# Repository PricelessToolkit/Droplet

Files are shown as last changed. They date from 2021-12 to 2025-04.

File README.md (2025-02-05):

🤗 Please consider subscribing to my [YouTube channel](https://www.youtube.com/@PricelessToolkit/videos)
Your subscription goes a long way in backing my work.



# Droplet
 ALL-IN-ONE Irrigation and monitoring system for ESPHome and Home Assistant.
 * Youtube How-To https://youtu.be/mCXTqONmpZk
 * Shop https://www.pricelesstoolkit.com

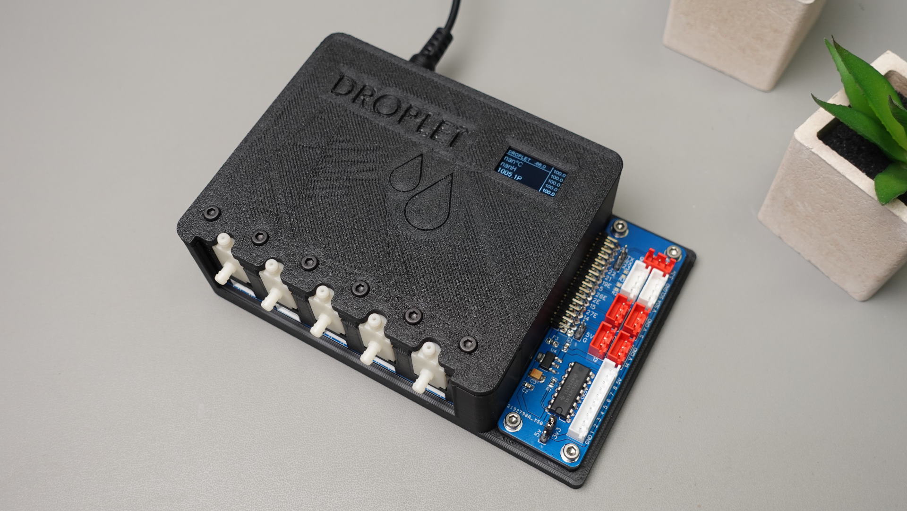
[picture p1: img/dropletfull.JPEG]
DROPLETFull
 

   ### Main Board

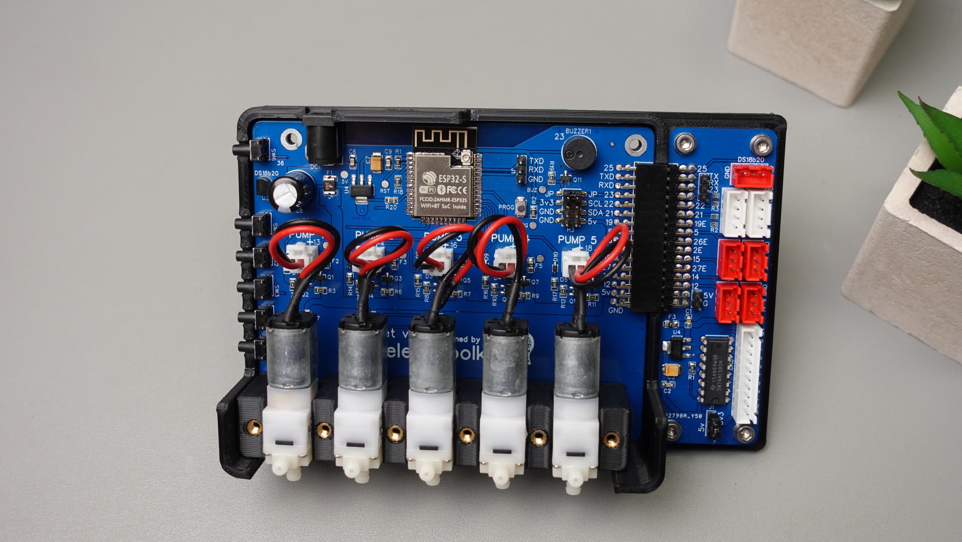
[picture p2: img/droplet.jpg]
DROPLET
 

 1. 5x Micro Pump outputs "5v"
 2. 5x Soil Moisture sensor inputs "Data-5v-GND" 'Data line pulled down with 1M ohm resistor' ( Data line MAX 3.3v !!!!! )
 3. Onboard Temperature sensor "DS18B20" https://esphome.io/components/sensor/dallas.html
 4. Onboard Buzzer "Buzzer port can be free up with jumper" https://esphome.io/components/rtttl.html?highlight=buzzer
 5. Breakout pins for connecting "i2c OLED Display" https://esphome.io/components/display/ssd1306.html?highlight=display
 6. 5x Buttons for manual Pumps controll
 7. 1x Button "Short press" for wake-up Oled "Long press" for general purpose. "2x Binary sensors available for HA"
 8. All pumps outputs and moisture sensor inputs have fuses
 9. Pins Which can be used "GPIO 19,5,26,2,15,27,14,12" and "1xi2c GPIO 21,22" "1xUART" "GPIO25 External port for DS18B20 TMP Sensor!!"
 
  ### Expansion Board v3

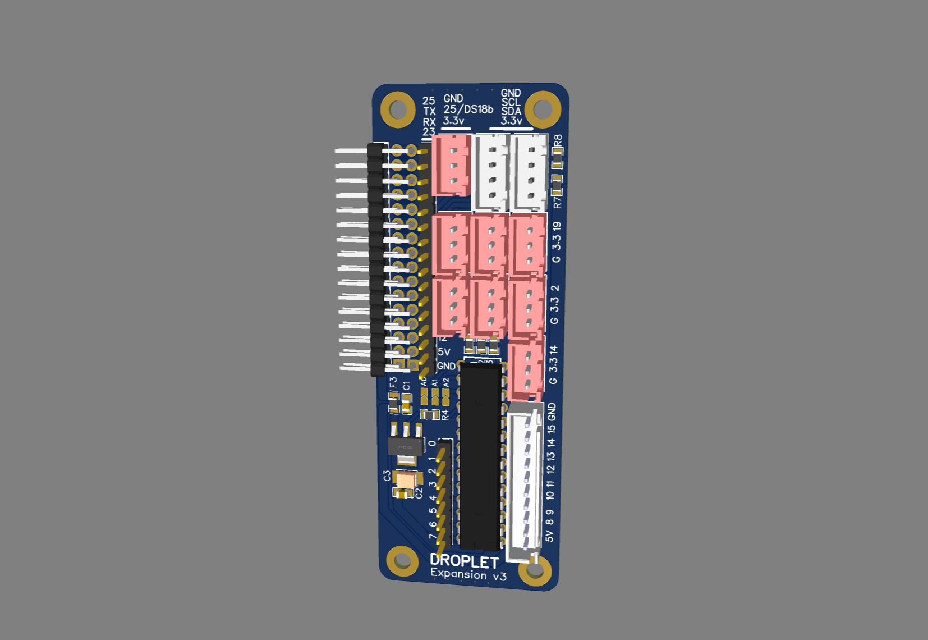
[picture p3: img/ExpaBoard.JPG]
ExpBoard
 

 1. 1x JST 10pin connector Outputs for 8 Relays  "MCP23017" Expander  https://esphome.io/components/mcp230xx.html
 2. 1x 8 Pin Header "MCP23017" Expander  https://esphome.io/components/mcp230xx.html
 3. 2x XH 4pin i2c (V, GPIO 21, GPIO 22 GND)
 4. 7x XH 3pin GPIO 19,5,26,2,15,27,14
 5. 1x XH 3pin for "DS18B20 TMP Sensors" (3.3v, GPIO 25, GND)
 6. 1x 1pin Header GPIO23 connected to buzzer. Buzzer port can be free up, "remove jumper JP"

 ## What sensors Droplet support ?
 ### Droplet support "Almost all sensors supported by ESPHome" https://esphome.io/index.html
 
 I connected and tested at the same time.
* 5x Pump
* 5x Moisture Sensor V2, 
* 2x "DS18B20" Temperature, 
* 1x BMP280 Temperature and Pressure, 
* 1x VL53L0x Distance Sensor, 
* 1x DHT Temperature and Humidity, 
* 8x Relays. 

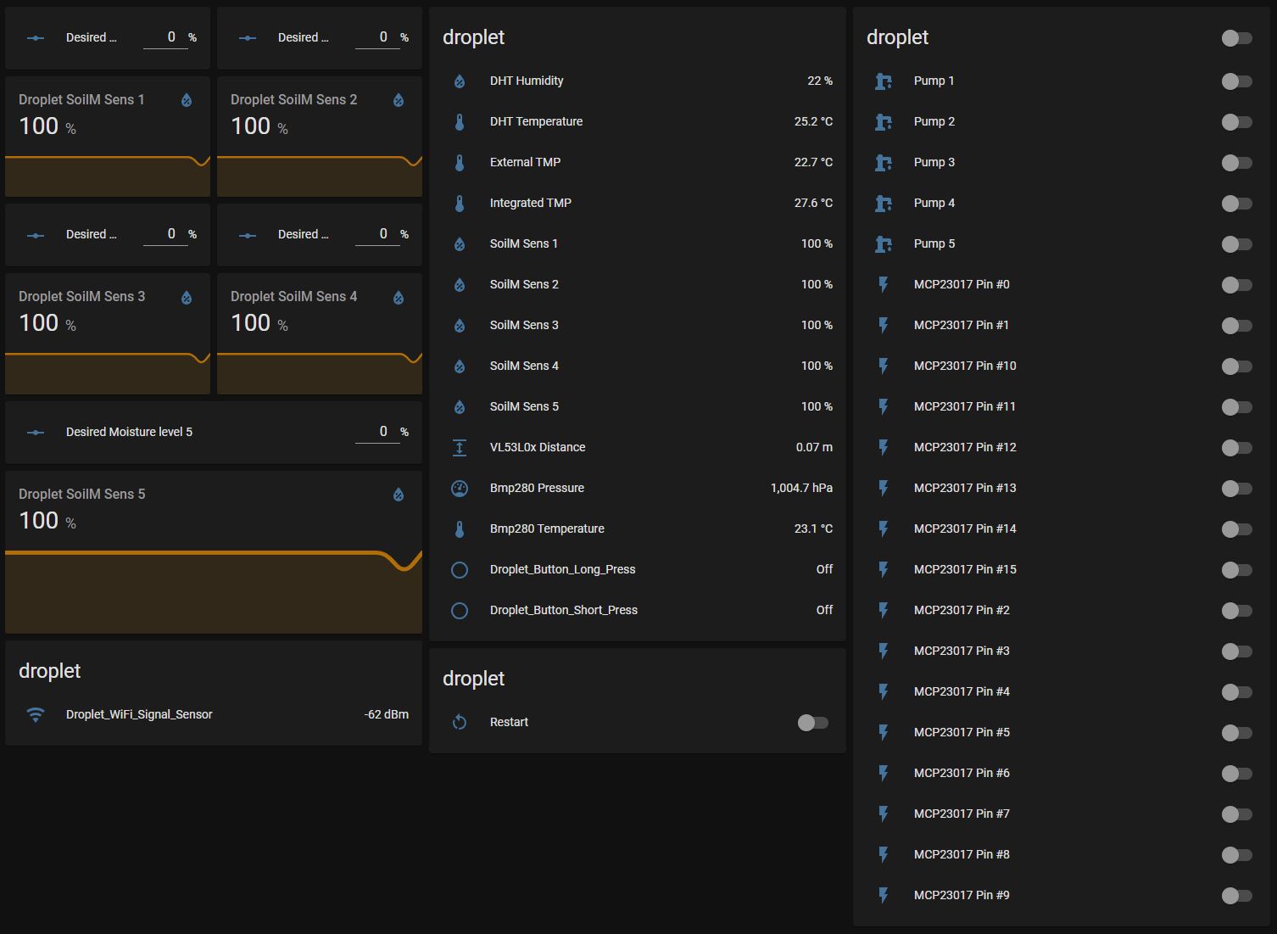
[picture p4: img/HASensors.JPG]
 

## First time setup

### WIFI Captive Portal

The captive portal component in ESPHome is a fallback mechanism for when connecting to the configured WiFi fails.
After 1 minute of unsuccessful WiFi connection attempts, the ESP will start a WiFi hotspot with the credentials
```
SSID: "Droplet Fallback Hotspot"
password: "password"
```

When you connect to the fallback network, the web interface should open automatically (see also login to network notifications).
If that does not work, you can also navigate to http://192.168.4.1/ manually in your browser.
In this web interface, you can manually override the WiFi settings of the device.
Additionally, you can upload a new firmware file to your node without having to use a USB cable for uploads.



### Reflashing via USB-UART adapter

First, you need to create in the ESPhome new device using the Droplet Config file "don't forget to change it to your needs" then compile it and download the ".bin" file. To upload it to the Droplet, we also need  "ESPHome Flasher" software

* Connect your USB-UART adapter to the Droplet Mainboard "GND, 3.3V, TX, RX"
* 
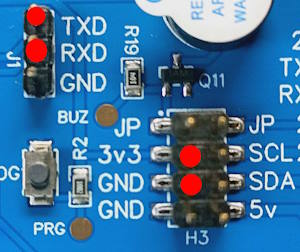
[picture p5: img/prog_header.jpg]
  
  
* Push the "PROG" button on the Droplet Mainboard "Don't release it"
* Plug the USB-UART adapter to the PC.
* Upload firmware via ESPHome Flasher.
* Release the "PROG" button.

## Setting the onboard DS18b20 temperature sensor

First of all we need to find out the address of the Onboard temperature sensor.
For example with this configuration: "which is already in the default config"

```yaml
one_wire: #https://esphome.io/components/one_wire
  - platform: gpio
    pin: GPIO25
```

In the log output (ensure the log level is set to at least debug), you’ll see something like this.



With the temperature sensor address identified in the log, we can now enable the Display component by uncomenting  this line.

```yaml
it.printf(5, 15, id(font3) ,"%.1f°C", id(intergratedtmp).state);
```

It should look like this in the full configuration.

```yaml
display: # More info https://esphome.io/components/display/ssd1306.html?highlight=1306         
- platform: ssd1306_i2c
  id: oled
  model: SSD1306 128x64
  address: 0x3C   # Oled Display Address
  lambda: |-
    it.printf(2, 0, id(font2), TextAlign::TOP_LEFT, "DROPLET");
    it.printf(61, 0, id(font2) ,"%.1f", id(dbm).state);
    it.line(0, 12, 98, 12);
    it.line(98, 0, 98, 64);
    it.printf(102, 0, id(font2) ,"%.1f", id(Soil1).state);
    it.printf(102, 12, id(font2) ,"%.1f", id(Soil2).state);
    it.printf(102, 24, id(font2) ,"%.1f", id(Soil3).state);
    it.printf(102, 36, id(font2) ,"%.1f", id(Soil4).state);
    it.printf(102, 48, id(font2) ,"%.1f", id(Soil5).state);
    it.printf(5, 15, id(font3) ,"%.1f°C", id(intergratedtmp).state);
#   it.printf(5, 30, id(font3) ,"%.1fH", id(dhthumidity).state);
#   it.printf(5, 45, id(font3) ,"%.1fP", id(pressure).state);

```

Now, uncomment the integrated temperature sensor configuration and add the address.

```yaml
  - platform: dallas_temp
    address: 0x6e3c......
    name: "${name} Integrated TMP"
    id: "intergratedtmp"
```
After adding it to the configuration, reinstall the firmware once more.

## Part List
> [!NOTE]
> !!! Sellers often change the type of pump, so the link may not be relevant. !!!
> The correct pump connector pitch is 2.54 mm.

* Power adapter 5v 2-3.5Ah Connector DC-005 2.0 - https://s.click.aliexpress.com/e/_DEsuOdV
* Oled Display - https://s.click.aliexpress.com/e/_DlkmoXv
* Water Pump "Model B JSB1523" 5V "Connector pitch 2.54mm" - https://s.click.aliexpress.com/e/_ok8vbDj
* Water Pump Datasheet - https://github.com/PricelessToolkit/Droplet/blob/main/Water_Pump_JSB1523008.pdf
* Silicone tube "inner diameters 3 and 4mm" - https://s.click.aliexpress.com/e/_DBnM9qL
* Heat Set Insert M3 X D4.6 X L4.5 - https://s.click.aliexpress.com/e/_9xbSZC
* Capacitive Soil Moisture Sensor "lottery may be working or defective" - https://s.click.aliexpress.com/e/_9Qz84W
* Cables with connectors for sensors and relays "pin pitch XH 2.54MM" - https://s.click.aliexpress.com/e/_DDpn7iB
* 3D Case "For those who live in France" you can order here - https://www.facebook.com/Upin3d
* Cable for soil moisture sensor https://s.click.aliexpress.com/e/_DDGNx5h

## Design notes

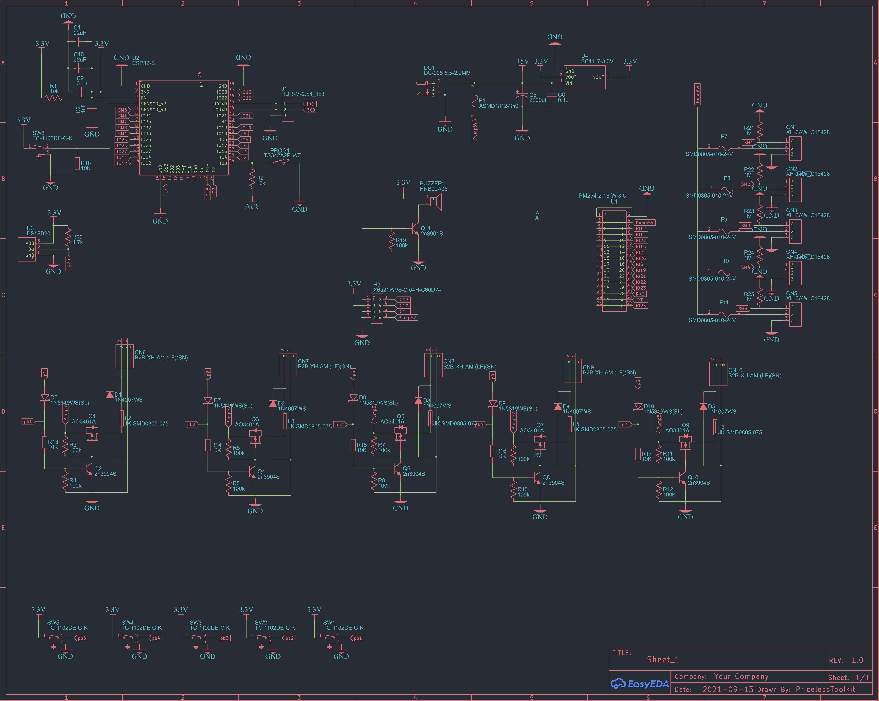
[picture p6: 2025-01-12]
Gerber/Droplet_Schematic.jpg

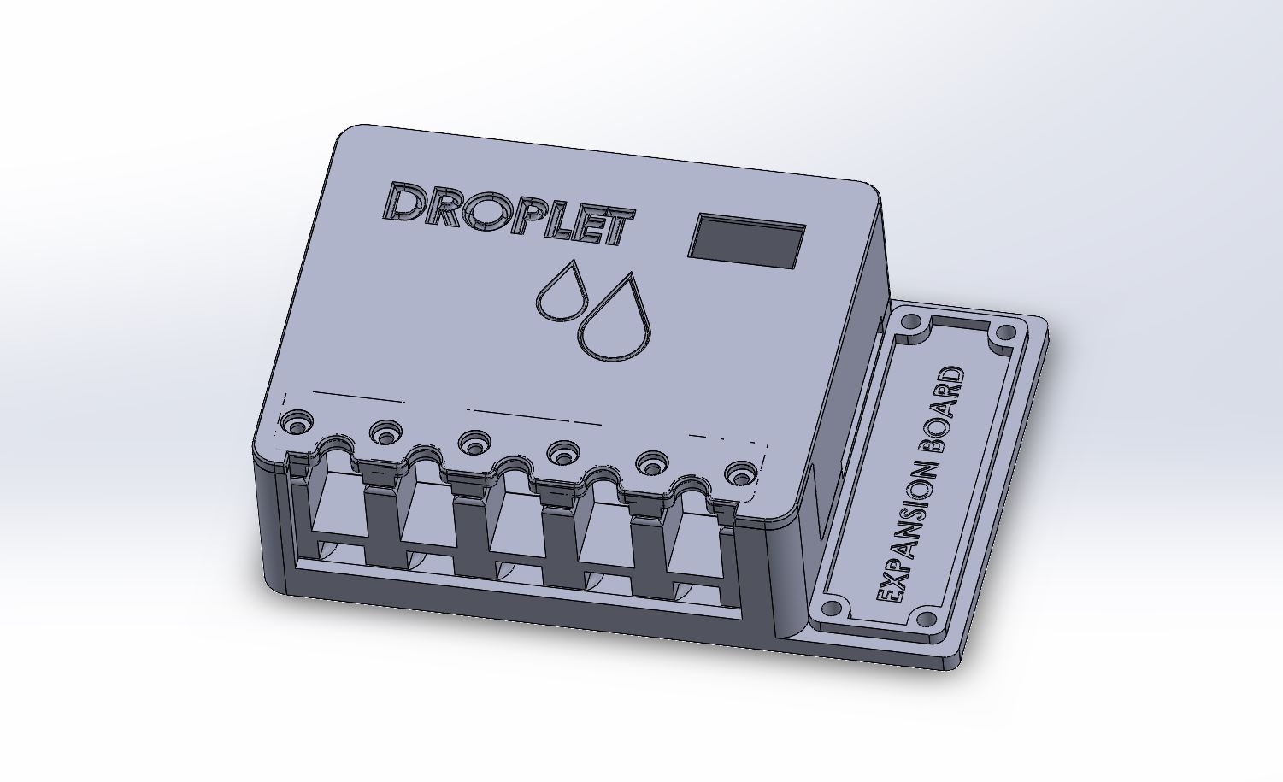
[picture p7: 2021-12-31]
img/Housing1.JPG

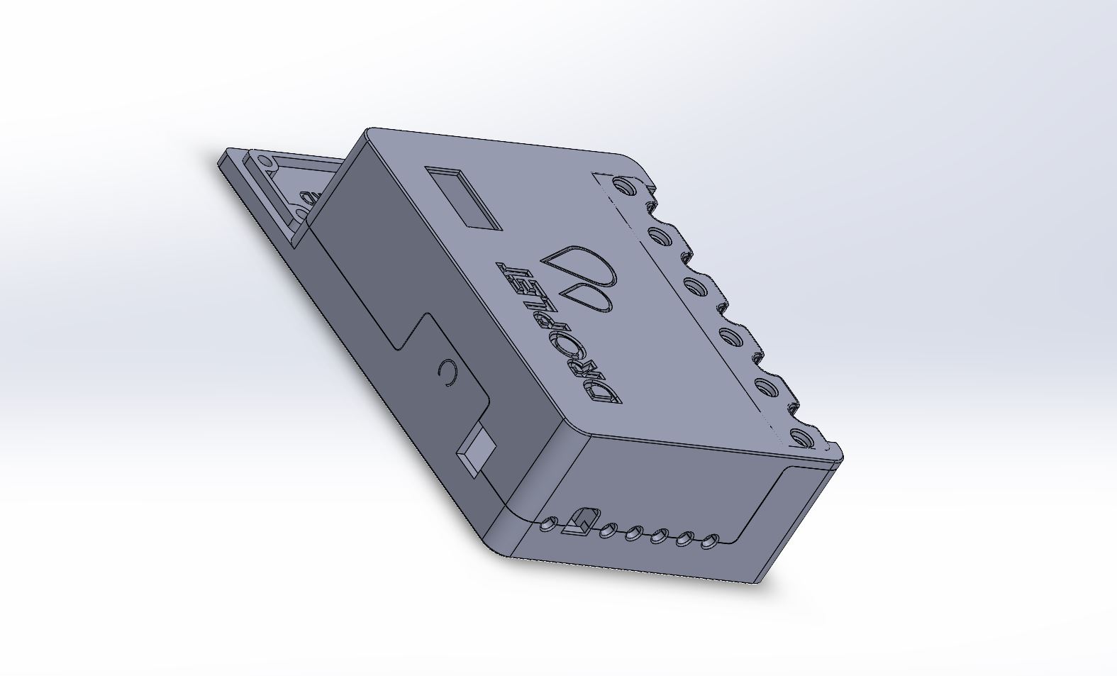
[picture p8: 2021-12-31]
img/Housing.JPG

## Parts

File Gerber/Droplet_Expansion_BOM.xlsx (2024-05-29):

Part IPN | Part Name | Quantity | Reference | Supplier_0 | SKU_0
CAP-000172-00 | Capacitor 0805_100nF_10%_50V_X7R - SMD/SMT ROHS | 1.0 | C1, C2 | LCSC Electronics | C49678
CAP-000162-00 | Tantalum Capacitor CASE-B-3528_22uF_10V_10% ROHS | 1.0 | C3 | LCSC Electronics | C7198
RES-000186-00 | Resistor 0805_4.7K_5%_150V_125mW - Surface Mount ROHS | 3.0 | R4, R7, R8 | LCSC | C26022
RES-000191-00 | Resistor 0805_10K_1%_150V_125mW - Surface Mount ROHS | 3.0 | R1, R2, R3 | LCSC | C115309
ICS-000241-00 | IO Expander MCP23017-E/SP 1.7MHZ I2C 28SDIP ROHS | 1.0 | U1 | Digi-Key | MCP23017-E/SP-ND
PWR-000089-00 | Voltage Regulator AMS1117-3.3V 1A 3.3V SOT-223 (LDO) ROHS | 1.0 | U1 | LCSC Electronics | C2688239
PRO-000185-00 | Resettable Fuse 0805_6V_750mA ROHS | 1.0 | F3 | LCSC | C369151
CON-000133-00 | Connector 1x3P XH 1 P=2.5mm Plugin ROHS | 8.0 | CN4, CN5, CN6, CN7, CN8, CN9, CN10, CN11 | LCSC Electronics | C168997
CON-000134-00 | Connector 1x4P XH 1 P=2.5mm Plugin ROHS | 2.0 | CN2, CN3 | LCSC Electronics | C125328
CON-000128-00 | Pin Header 2x16P 250V 3A P=2.54mm Gold Right-Angle Plugin ROHS | 1.0 | H1 | LCSC Electronics | C97095
CON-000141-00 | Pin Header 1x8P P=2.54mm Straight Plugin ROHS | 1.0 | J7 | LCSC Electronics | C190820
CON-000332-00 | Pin Header 1x16P P=2.54mm 3A Straight Plugin ROHS | 1.0 | J1 | LCSC | C2905491
CON-000333-00 | Connector 1x10P_2.5mm_3A Straight Plugin ROHS | 1.0 | CN1 | LCSC | C2833905

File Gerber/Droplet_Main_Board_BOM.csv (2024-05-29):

ID | Name | Designator | Footprint | Quantity | Manufacturer Part | Manufacturer
1 | CONN-TH_B2B-XH-AM-LF-SN | U6,U7,U8,U9,U10 | CONN-TH_B2B-XH-AM-LF-SN | 5 | - | JST Sales America
3 | PM254-2-16-W-8.5 | U1 | HDR-TH_32P-P2.54-H-F-R2-C16-W8.5 | 1 | PM254-2-16-W-8.5 | HCTL(华灿天禄)
4 | TS342A2P-WZ | PROG1 | SW-SMD_L4.0-W2.9-LS5.0 | 1 | TS342A2P-WZ | SHOU HAN
5 | TC-1102DE-C-K | SW1,SW2,SW3,SW4,SW5,SW6 | SW-TH_TC-1102DE-C-K | 6 | TC-1102DE-C-K | XKB Enterprise
6 | HDR-M-2.54_1x3 | J1 | HDR-M-2.54_1X3 | 1 | PZ200V-11-03P | XFCN
7 | 4.7k | R20 | R0805 | 1 | 0805W8J0472T5E | UniOhm
8 | 1M | R21,R22,R23,R24,R25 | R0805 | 5 | 0805W8J0105T5E | UniOhm
9 | SC1117-3.3V | U4 | SOT-223_L6.5-W3.5-P2.30-LS7.0-BR | 1 | SC1117-3.3V | FM
10 | 22uF | C7 | CAP-SMD_L3.5-W2.8-R-RD | 1 | TAJB226K010RNJ | AVX
11 | HNB09A05 | BUZZER1 | BUZ-TH_BD9.6-P5.00-D0.7-FD | 1 | HNB09A05 | HNDZ
12 | X6521WVS-2*04H-C60D74 | H3 | HDR-SMD_8P-P2.54-V-M-R2-C5-S7.4 | 1 | X6521WVS-2*04H-C60D74 | XKB Connectivity
13 | 2n3904S | Q11,Q2,Q4,Q6,Q8,Q10 | SOT-23-3_L2.9-W1.3-P1.90-LS2.4-TR | 6 | 2n3904S-RTK/PS | KEC
14 | 100k | R19,R3,R4,R5,R6,R7,R8,R9,R10,R11,R12 | R0805 | 11 | RS-05K104JT | FH
15 | 10K | R18,R13,R14,R15,R16,R17 | R0805 | 6 | RS-05K1002FT | FH
16 | DS18B20 | U3 | TO-92-3_L4.9-W3.7-P1.27-L | 1 | DS18B20 | Youtai Semiconductor Co., Ltd.
17 | 1N5819WS(SL) | D6,D7,D8,D9,D10 | SOD-323_L1.7-W1.3-LS2.7-RD | 5 | 1N5819WS(SL) | KEXIN
18 | SMD0805-010-24V | F8,F9,F10,F11,F7 | F0805 | 5 | SMD0805-010-24V | TECHFUSE
19 | 0.1u | C6,C9 | C0805 | 2
20 | JK-SMD0805-075 | F2,F3,F4,F5,F6 | F0805 | 5 | JK-SMD0805-075 | Jinrui Electronic Materials Co.
21 | 2200uF | C8 | CAP-TH_BD10.0-P5.00-D1.0-FD | 1 | EEUFS0J222 | PANASONIC
22 | DC-005 5.5-2.0MM | DC1 | DC-IN-TH_DC-5520-1 | 1 | DC-005 5.5-2.0MM | BOOMELE
23 | 10k | R1,R2 | R0805 | 2 | RS-05K1002FT | FH
24 | XH-3AW_C18428 | CN1,CN2,CN3,CN4,CN5 | CONN-TH_3P-P2.50_XH-3A | 5 | XH-3AW | BOOMELE
25 | AO3401A | Q1,Q3,Q5,Q7,Q9 | SOT-23_L2.9-W1.3-P1.90-LS2.4-BR | 5 | AO3401A | AOS
26 | 1N4007WS | D1,D2,D3,D4,D5 | SOD-323_L1.8-W1.3-LS2.5-RD | 5 | 1N4007WS | (MDD) Jiangsu Yutai Elec
27 | ESP32-S | U2 | WIRELM-SMD_ESP32-S | 1 | ESP32-S | Ai-Thinker
28 | ASMD1812-350 | F1 | F1812 | 1 | ASMD1812-350 | JDTFUSE

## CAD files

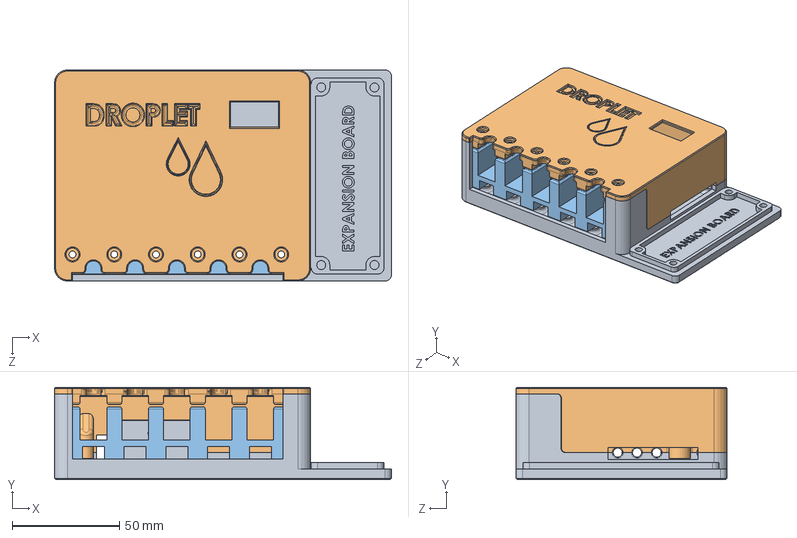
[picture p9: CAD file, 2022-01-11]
3D/Assem.SLDASM
157.1 x 43.0 x 98.4 mm
Housing_battom
Cover_full_Part
Pump_Holder_Down

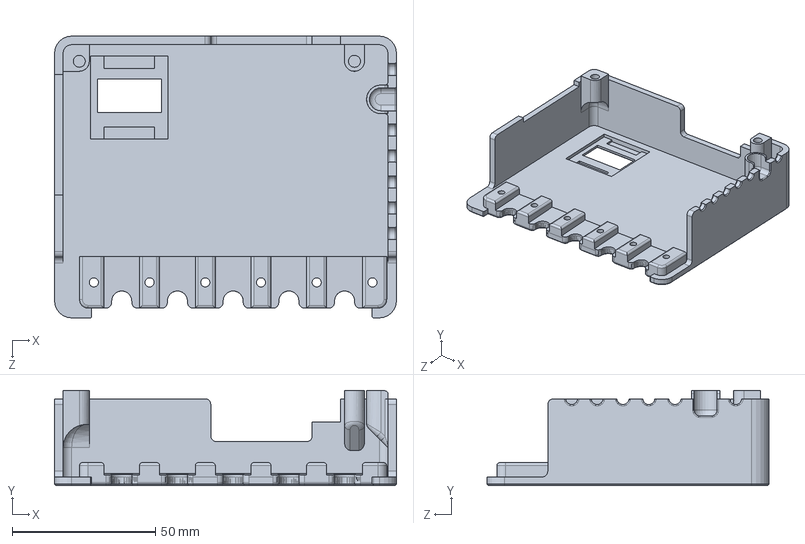
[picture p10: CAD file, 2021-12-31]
3D/Cover_full_Part.SLDPRT
119.4 x 33.2 x 98.4 mm

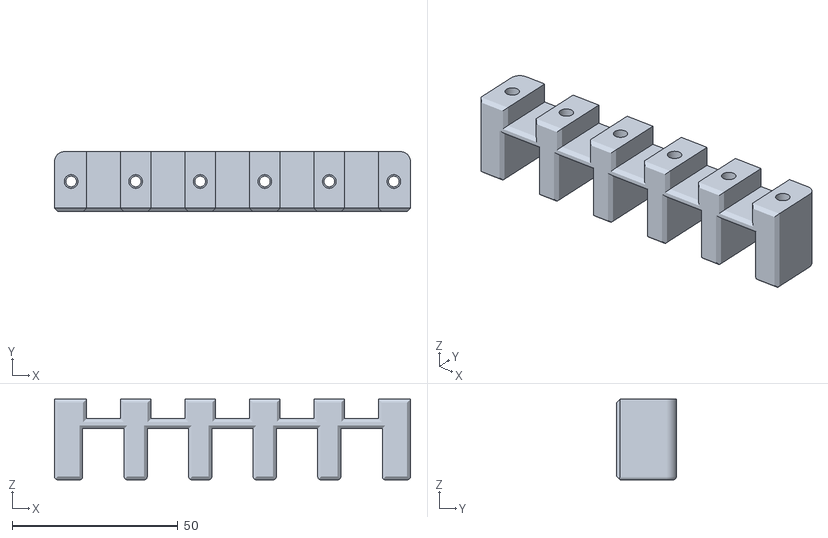
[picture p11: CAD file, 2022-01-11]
3D/Pumps_Holder.STL
107.3 x 18.0 x 24.4

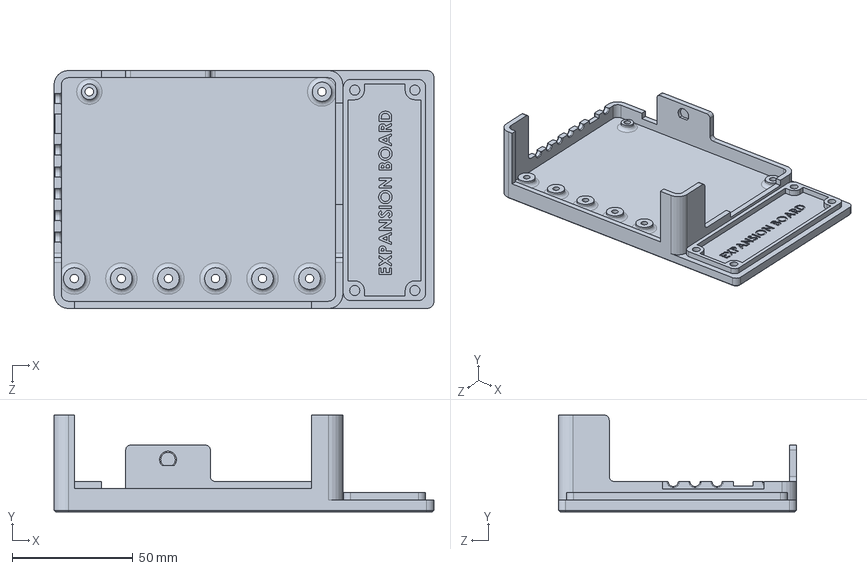
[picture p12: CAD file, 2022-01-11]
3D/Housing_battom.SLDPRT
157.1 x 40.0 x 98.4 mm

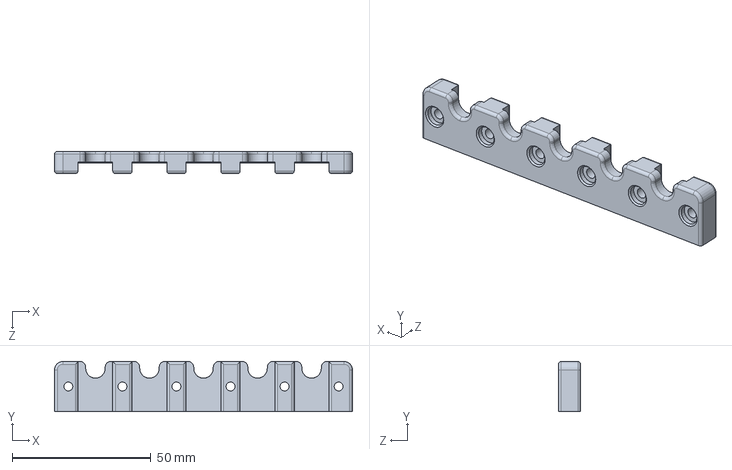
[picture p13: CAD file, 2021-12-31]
3D/Pump_Holder_UP.SLDPRT
107.3 x 18.0 x 8.00 mm

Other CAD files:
3D/Assem_Cover_full.SLDASM
3D/Pump_Holder_Down.SLDPRT

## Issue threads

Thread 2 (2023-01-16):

What cable for Soil Sensors

lordratner, 2023-01-16:
Hi! I just got my droplet set up, and it is excellent! Very cool.

What cables do you use for extending the connection to the soil sensors? I don't know what the plug is called, so I don't know what to search for.

Thanks!

PricelessToolkit, 2023-01-16:
Hi, I'm very glad you liked it!!
The droplet has ( JST 2.54mm pitch 3-pin ) connector, and for the sensor, it depends on your sensor :)  if you use a sensor like mine, it's JST 2.54mm pitch 3-pin too. You can buy a cable for (3d printers "End Stops" )  https://s.click.aliexpress.com/e/_DErXOBt  just look at the polarity and pin order!!!!!  "can be easily swapped if needed"  If it's not difficult, leave a review in the store :) Thanks!!

PricelessToolkit, 2023-01-16:
I forgot to say if the cable is long better to find a shielded cable.

Closed 2023-01-18.

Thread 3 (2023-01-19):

Short vs Long button press

lordratner, 2023-01-19:
Current behavior: When you press and hold the top button, droplet_button_short_press comes on, then droplet_button_long_press comes on.

This makes it difficult to have different automations for short and long presses, since the short press will trigger any time you long press.

Instead, droplet_button_short_press should only come on when the button is released quickly.

Thoughts?

lordratner, 2023-01-19:
From ESPHome:
on_click
This automation will be triggered when a button is pressed down for a time period of length min_length to max_length. Any click longer or shorter than this will not trigger the automation. The automation is therefore also triggered on the falling edge of the signal.

So I'd recommend something like this:

```
binary_sensor:
  - platform: gpio
    name: "${name} Button Short Press"
    pin:
      number: 36
    on_click:
    - min_length: 10ms
      max_length: 499ms
      then:
        - lambda: id(oled).turn_on();
        - delay: 20s
        - lambda: id(oled).turn_off();

  - platform: gpio
    name: "${name} Button Long Press"
    pin:
      number: 36
    on_click:
    - min_length: 500ms
      max_length: 1000ms
```

I think you could also combine it into one binary sensor per the documents, but then you wouldn't have two entities in HA.

PricelessToolkit, 2023-01-20:
Hi, yes, the idea is good, thanks, I will add it to the config, then people will choose what is convenient for them.
I made it that way because in my use case, I don't need 2 automation. it is more important for me to see the data on the OLED. and I didn't want to click to activate the screen and then click again to trigger the automation. May I know what kind of automation you use for this button?

lordratner, 2023-01-20:
For the long press I toggle my grow light.

For the short press I want to toggle the fan.

After thinking about it, I think better timings would be
    - min_length: 10ms
      max_length: 250ms

for the short press and

    - min_length: 250ms
      max_length: 2000ms

for the long press.

Closed 2023-04-20.

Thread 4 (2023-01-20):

A couple questions

lordratner, 2023-01-20:
I'll put these here since the discussion section is not activated for this repo.

1. How do you keep a pump on in home assistant? On the droplet I can hold the pump button, but in HA the pump only stays on for a second or less.

2. Would you consider a bulk watering routine? I have my droplet feeding a seedling trays with 50 plants each. I would like to water them by waiting for the moisture level to get down to a certain point, then trigger the pump for xx seconds to feed the entire tray. If I only do multiple short bursts of water, the plants closest to the droplet tube get all the water.

Right now I plan to set the "desired moisture level" to 0% to disable the automatic pumping from droplet. Then in HA I will set an automation that will trigger when moisture gets below xx%, run the pump for xx seconds (probably 30 to start), wait xxx seconds, then check moisture levels again.

It could be nice to have two watering modes, immediate and bulk:

Immediate mode: Current behavior, when moisture drops below set point, pump runs in short bursts until moisture is above set point. User inputs for each zone:

- desired moisture level

Bulk Mode: When moisture drops below set point, pump runs for xx seconds, then waits for a few minutes, then repeats until moisture is above a target level
User Inputs for each zone:

- Trigger moisture level
- pump duration
- Target Moisture level

Thoughts? I'm really enjoying this device, thank you for making it!

PricelessToolkit, 2023-01-21:
You can change pumps "ON Time" by changing "update_interval: 2s" in esphome config, or comment out  "Comparison Sens1,2,3,4,5 sections" and activate your pumps by Home Assistant automation.

PricelessToolkit, 2023-01-21:
I'll try to explain it differently

1. if you want to control the pumps from Home Assistant then  comment out "Comparison Sens1,2,3,4,5 sections"
but keep in mind if you restart the home assistant during the watering the pumps will not stop!

2. I think  is better to choose the "time" of saturation of the soil with water, then change update_interval: XXs
it's more reliable, it won't overflow

lordratner, 2023-01-21:
Ok I'll try that. What's the best way to add droplet to EspHome? I just added it as an integration in HA, but that doesn't let me update the configuration. Do I need to use a USB cable?

PricelessToolkit, 2023-01-21:
1. Create a new config in ESPhome
2. Compile it and Download the XXXX.bin file
3. Turn OFF your home WIFI (so that Droplet does not find where to connect)
4. Connect to "Droplet  Fallback Hotspot" via WIFI and upload the XXXX.bin file.
  https://github.com/PricelessToolkit/Droplet#first-time-setup

lordratner, 2023-01-21:
Ok great, got it connected. I'll start fiddling around see what I come up with. Thanks!

Closed 2023-07-18.

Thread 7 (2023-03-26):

Instructions missing for removing the JP to JP jumper for it to actually flash

nstrelow, 2023-03-26:
I finally got all the parts and components and try to flash the Droplet.

I followed the flashing instructions, but only after removing the preinstalled jumper from JP to JP, was it able to flash.

What is this jumper doing and should I reinstall it ?

PricelessToolkit, 2023-03-26:
Hi, Yes reinsert it. Jumper connects pin23 to Buzzer, if u remove it you can use pin23 externally "from the expansion board".

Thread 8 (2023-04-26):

What kind of pump do you recommend?

facos86, 2023-04-26:
Hi, since there is a shortage of pump on your website, which water pump do you recommend?
Regards

PricelessToolkit, 2023-04-26:
Hi, on the project main page "Pump 2 - https://s.click.aliexpress.com/e/_DdU508h"

facos86, 2023-04-28:
THanks!

Closed 2023-04-28.

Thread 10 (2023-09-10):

Publish schematics

namero999, 2023-09-10:
Hello, I'm impressed by this project, it also addresses a lot of the questions I have around custom PCB design (such as integrating a custom ESP32 module). I think the schematics would be a terrific learning material. Is there any chance that you could publish them as well?

PricelessToolkit, 2023-09-19:
schematic is made with the idea that it remains private. it's not for public sensitive eyes, I did a disgusting job :).  Nothing complicated in circuit design, search on the Internet for how to control a motor using a MOSFET and that’s it.

Closed 2023-09-21.

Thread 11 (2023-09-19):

3D files for ptinting the case

stefancvetkovic, 2023-09-19:
Hello,
I received the main board, while external board I am assembling right now.
Can you please upload also 3D case for extender and main board?

Thanks

PricelessToolkit, 2023-09-19:
Hi, I'm glad you finally received the package! All 3D files are available in the 3D folder.

Closed 2023-09-21.

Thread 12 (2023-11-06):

pillow not found for fonts

stefancvetkovic, 2023-11-06:
Hello Im having first steps, and for some reason, I cant build esphome through CLI on my Windows Im getting an error:
Failed config

font: [source .\droplet.yml:56]

  Please update your pillow installation to at least 4.0.x. (pip install -U pillow).
  - file: arial.ttf
    id: font1
    size: 8

I have already installed pillow package with version
Name: Pillow
Version: 10.1.0

Do i need to downgrade to exact 4.0 version or? Do you know maybe?

Thanks

stefancvetkovic, 2023-11-06:
Also what is the default password for OTA update?

PricelessToolkit, 2023-11-06:
Hi,
https://github.com/PricelessToolkit/Droplet/blob/main/Config/ESPHome/droplet.yaml
```
ota:
  password: "bfec11234xsfea57e1b5d3b985cfe06c"
```
let me check it with the new ESPHome version.

PricelessToolkit, 2023-11-06:
With the latest ESPhome compiled without a problem, I can't say anything about version requirements.

```
INFO ESPHome 2023.10.6
INFO Reading configuration /config/esphome/droplet.yaml...
WARNING GPIO5 is a Strapping PIN and should be avoided.
Attaching external pullup/down resistors to strapping pins can cause unexpected failures.
See https://esphome.io/guides/faq.html#why-am-i-getting-a-warning-about-strapping-pins
INFO Generating C++ source...
INFO Core config or version changed, cleaning build files...
INFO Compiling app...
Processing droplet (board: esp32dev; framework: arduino; platform: platformio/espressif32@5.4.0)
--------------------------------------------------------------------------------
Library Manager: Installing esphome/AsyncTCP-esphome @ 2.0.1
INFO Installing esphome/AsyncTCP-esphome @ 2.0.1
Downloading  [####################################]  100%
Unpacking  [####################################]  100%
Library Manager: AsyncTCP-esphome@2.0.1 has been installed!
INFO AsyncTCP-esphome@2.0.1 has been installed!
Library Manager: Installing esphome/ESPAsyncWebServer-esphome @ 3.1.0
INFO Installing esphome/ESPAsyncWebServer-esphome @ 3.1.0
Downloading  [####################################]  100%
Unpacking  [####################################]  100%
Library Manager: ESPAsyncWebServer-esphome@3.1.0 has been installed!
INFO ESPAsyncWebServer-esphome@3.1.0 has been installed!
Library Manager: Resolving dependencies...
INFO Resolving dependencies...
HARDWARE: ESP32 240MHz, 320KB RAM, 4MB Flash
 - toolchain-xtensa-esp32 @ 8.4.0+2021r2-patch5
Dependency Graph
|-- AsyncTCP-esphome @ 2.0.1
|-- WiFi @ 2.0.0
|-- FS @ 2.0.0
|-- Update @ 2.0.0
|-- ESPAsyncWebServer-esphome @ 3.1.0
|-- DNSServer @ 2.0.0
|-- ESPmDNS @ 2.0.0
|-- Wire @ 2.0.0
Compiling .pioenvs/droplet/src/esphome/components/adc/adc_sensor.cpp.o
Compiling .pioenvs/droplet/src/esphome/components/api/api_connection.cpp.o
Compiling .pioenvs/droplet/src/esphome/components/api/api_frame_helper.cpp.o
Compiling .pioenvs/droplet/src/esphome/components/api/api_pb2.cpp.o
Compiling .pioenvs/droplet/src/esphome/components/api/api_pb2_service.cpp.o
Compiling .pioenvs/droplet/src/esphome/components/api/api_server.cpp.o
Compiling .pioenvs/droplet/src/esphome/components/api/list_entities.cpp.o
Compiling .pioenvs/droplet/src/esphome/components/api/proto.cpp.o
Compiling .pioenvs/droplet/src/esphome/components/api/subscribe_state.cpp.o
Compiling .pioenvs/droplet/src/esphome/components/api/user_services.cpp.o
Compiling .pioenvs/droplet/src/esphome/components/binary_sensor/automation.cpp.o
Compiling .pioenvs/droplet/src/esphome/components/binary_sensor/binary_sensor.cpp.o
Compiling .pioenvs/droplet/src/esphome/components/binary_sensor/filter.cpp.o
Compiling .pioenvs/droplet/src/esphome/components/bmp280/bmp280.cpp.o
Compiling .pioenvs/droplet/src/esphome/components/captive_portal/captive_portal.cpp.o
Compiling .pioenvs/droplet/src/esphome/components/dallas/dallas_component.cpp.o
Compiling .pioenvs/droplet/src/esphome/components/dallas/esp_one_wire.cpp.o
Compiling .pioenvs/droplet/src/esphome/components/dht/dht.cpp.o
Compiling .pioenvs/droplet/src/esphome/components/display/display.cpp.o
Compiling .pioenvs/droplet/src/esphome/components/display/display_buffer.cpp.o
Compiling .pioenvs/droplet/src/esphome/components/display/rect.cpp.o
Compiling .pioenvs/droplet/src/esphome/components/esp32/core.cpp.o
Compiling .pioenvs/droplet/src/esphome/components/esp32/gpio.cpp.o
Compiling .pioenvs/droplet/src/esphome/components/esp32/preferences.cpp.o
Compiling .pioenvs/droplet/src/esphome/components/font/font.cpp.o
Compiling .pioenvs/droplet/src/esphome/components/gpio/binary_sensor/gpio_binary_sensor.cpp.o
Compiling .pioenvs/droplet/src/esphome/components/gpio/switch/gpio_switch.cpp.o
Compiling .pioenvs/droplet/src/esphome/components/homeassistant/sensor/homeassistant_sensor.cpp.o
Compiling .pioenvs/droplet/src/esphome/components/i2c/i2c.cpp.o
Compiling .pioenvs/droplet/src/esphome/components/i2c/i2c_bus_arduino.cpp.o
Compiling .pioenvs/droplet/src/esphome/components/i2c/i2c_bus_esp_idf.cpp.o
Compiling .pioenvs/droplet/src/esphome/components/ledc/ledc_output.cpp.o
Compiling .pioenvs/droplet/src/esphome/components/logger/logger.cpp.o
Compiling .pioenvs/droplet/src/esphome/components/mcp23017/mcp23017.cpp.o
Compiling .pioenvs/droplet/src/esphome/components/mcp23x17_base/mcp23x17_base.cpp.o
Compiling .pioenvs/droplet/src/esphome/components/mcp23xxx_base/mcp23xxx_base.cpp.o
Compiling .pioenvs/droplet/src/esphome/components/md5/md5.cpp.o
Compiling .pioenvs/droplet/src/esphome/components/mdns/mdns_component.cpp.o
Compiling .pioenvs/droplet/src/esphome/components/mdns/mdns_esp32.cpp.o
Compiling .pioenvs/droplet/src/esphome/components/mdns/mdns_esp8266.cpp.o
Compiling .pioenvs/droplet/src/esphome/components/mdns/mdns_host.cpp.o
Compiling .pioenvs/droplet/src/esphome/components/mdns/mdns_libretiny.cpp.o
Compiling .pioenvs/droplet/src/esphome/components/mdns/mdns_rp2040.cpp.o
Compiling .pioenvs/droplet/src/esphome/components/network/util.cpp.o
Compiling .pioenvs/droplet/src/esphome/components/ota/ota_backend_arduino_esp32.cpp.o
Compiling .pioenvs/droplet/src/esphome/components/ota/ota_backend_arduino_esp8266.cpp.o
Compiling .pioenvs/droplet/src/esphome/components/ota/ota_backend_arduino_libretiny.cpp.o
Compiling .pioenvs/droplet/src/esphome/components/ota/ota_backend_arduino_rp2040.cpp.o
Compiling .pioenvs/droplet/src/esphome/components/ota/ota_backend_esp_idf.cpp.o
Compiling .pioenvs/droplet/src/esphome/components/ota/ota_component.cpp.o
Compiling .pioenvs/droplet/src/esphome/components/output/automation.cpp.o
Compiling .pioenvs/droplet/src/esphome/components/output/float_output.cpp.o
Compiling .pioenvs/droplet/src/esphome/components/restart/switch/restart_switch.cpp.o
Compiling .pioenvs/droplet/src/esphome/components/rtttl/rtttl.cpp.o
Compiling .pioenvs/droplet/src/esphome/components/sensor/automation.cpp.o
Compiling .pioenvs/droplet/src/esphome/components/sensor/filter.cpp.o
Compiling .pioenvs/droplet/src/esphome/components/sensor/sensor.cpp.o
Compiling .pioenvs/droplet/src/esphome/components/socket/bsd_sockets_impl.cpp.o
Compiling .pioenvs/droplet/src/esphome/components/socket/lwip_raw_tcp_impl.cpp.o
Compiling .pioenvs/droplet/src/esphome/components/socket/lwip_sockets_impl.cpp.o
Compiling .pioenvs/droplet/src/esphome/components/socket/socket.cpp.o
Compiling .pioenvs/droplet/src/esphome/components/ssd1306_base/ssd1306_base.cpp.o
Compiling .pioenvs/droplet/src/esphome/components/ssd1306_i2c/ssd1306_i2c.cpp.o
Compiling .pioenvs/droplet/src/esphome/components/switch/automation.cpp.o
Compiling .pioenvs/droplet/src/esphome/components/switch/switch.cpp.o
Compiling .pioenvs/droplet/src/esphome/components/template/sensor/template_sensor.cpp.o
Compiling .pioenvs/droplet/src/esphome/components/vl53l0x/vl53l0x_sensor.cpp.o
Compiling .pioenvs/droplet/src/esphome/components/web_server_base/web_server_base.cpp.o
Compiling .pioenvs/droplet/src/esphome/components/wifi/wifi_component.cpp.o
Compiling .pioenvs/droplet/src/esphome/components/wifi/wifi_component_esp32_arduino.cpp.o
Compiling .pioenvs/droplet/src/esphome/components/wifi/wifi_component_esp8266.cpp.o
Compiling .pioenvs/droplet/src/esphome/components/wifi/wifi_component_esp_idf.cpp.o
Compiling .pioenvs/droplet/src/esphome/components/wifi/wifi_component_libretiny.cpp.o
Compiling .pioenvs/droplet/src/esphome/components/wifi/wifi_component_pico_w.cpp.o
Compiling .pioenvs/droplet/src/esphome/components/wifi_signal/wifi_signal_sensor.cpp.o
Compiling .pioenvs/droplet/src/esphome/core/application.cpp.o
Compiling .pioenvs/droplet/src/esphome/core/color.cpp.o
Compiling .pioenvs/droplet/src/esphome/core/component.cpp.o
Compiling .pioenvs/droplet/src/esphome/core/component_iterator.cpp.o
Compiling .pioenvs/droplet/src/esphome/core/controller.cpp.o
Compiling .pioenvs/droplet/src/esphome/core/entity_base.cpp.o
Compiling .pioenvs/droplet/src/esphome/core/helpers.cpp.o
Compiling .pioenvs/droplet/src/esphome/core/log.cpp.o
Compiling .pioenvs/droplet/src/esphome/core/scheduler.cpp.o
Compiling .pioenvs/droplet/src/esphome/core/string_ref.cpp.o
Compiling .pioenvs/droplet/src/esphome/core/time.cpp.o
Compiling .pioenvs/droplet/src/esphome/core/util.cpp.o
Compiling .pioenvs/droplet/src/main.cpp.o
Building .pioenvs/droplet/bootloader.bin
Creating esp32 image...
Successfully created esp32 image.
Generating partitions .pioenvs/droplet/partitions.bin
Compiling .pioenvs/droplet/lib789/AsyncTCP-esphome/AsyncTCP.cpp.o
/config/esphome/droplet.yaml: In lambda function:
/config/esphome/droplet.yaml:240:22: warning: control reaches end of non-void function [-Wreturn-type]
         id(pump1).toggle();
         ~~~~~~~~~~~~~^~
/config/esphome/droplet.yaml: In lambda function:
/config/esphome/droplet.yaml:253:22: warning: control reaches end of non-void function [-Wreturn-type]
         id(pump2).toggle();
         ~~~~~~~~~~~~~^~
/config/esphome/droplet.yaml: In lambda function:
/config/esphome/droplet.yaml:266:22: warning: control reaches end of non-void function [-Wreturn-type]
         id(pump3).toggle();
         ~~~~~~~~~~~~~^~
/config/esphome/droplet.yaml: In lambda function:
/config/esphome/droplet.yaml:278:22: warning: control reaches end of non-void function [-Wreturn-type]
         id(pump4).toggle();
         ~~~~~~~~~~~~~^~
/config/esphome/droplet.yaml: In lambda function:
/config/esphome/droplet.yaml:291:22: warning: control reaches end of non-void function [-Wreturn-type]
         id(pump5).toggle();
         ~~~~~~~~~~~~~^~
Archiving .pioenvs/droplet/lib789/libAsyncTCP-esphome.a
Compiling .pioenvs/droplet/lib64d/WiFi/WiFi.cpp.o
Compiling .pioenvs/droplet/lib64d/WiFi/WiFiAP.cpp.o
Compiling .pioenvs/droplet/lib64d/WiFi/WiFiClient.cpp.o
Compiling .pioenvs/droplet/lib64d/WiFi/WiFiGeneric.cpp.o
Compiling .pioenvs/droplet/lib64d/WiFi/WiFiMulti.cpp.o
Compiling .pioenvs/droplet/lib64d/WiFi/WiFiSTA.cpp.o
Compiling .pioenvs/droplet/lib64d/WiFi/WiFiScan.cpp.o
Compiling .pioenvs/droplet/lib64d/WiFi/WiFiServer.cpp.o
Compiling .pioenvs/droplet/lib64d/WiFi/WiFiUdp.cpp.o
Compiling .pioenvs/droplet/lib01c/FS/FS.cpp.o
Archiving .pioenvs/droplet/lib64d/libWiFi.a
Compiling .pioenvs/droplet/lib01c/FS/vfs_api.cpp.o
Compiling .pioenvs/droplet/libbc6/Update/HttpsOTAUpdate.cpp.o
Archiving .pioenvs/droplet/lib01c/libFS.a
Compiling .pioenvs/droplet/libbc6/Update/Updater.cpp.o
Compiling .pioenvs/droplet/lib590/ESPAsyncWebServer-esphome/AsyncEventSource.cpp.o
Archiving .pioenvs/droplet/libbc6/libUpdate.a
Compiling .pioenvs/droplet/lib590/ESPAsyncWebServer-esphome/AsyncWebSocket.cpp.o
Compiling .pioenvs/droplet/lib590/ESPAsyncWebServer-esphome/WebAuthentication.cpp.o
Compiling .pioenvs/droplet/lib590/ESPAsyncWebServer-esphome/WebHandlers.cpp.o
Compiling .pioenvs/droplet/lib590/ESPAsyncWebServer-esphome/WebRequest.cpp.o
Compiling .pioenvs/droplet/lib590/ESPAsyncWebServer-esphome/WebResponses.cpp.o
Compiling .pioenvs/droplet/lib590/ESPAsyncWebServer-esphome/WebServer.cpp.o
Compiling .pioenvs/droplet/lib333/DNSServer/DNSServer.cpp.o
Archiving .pioenvs/droplet/lib590/libESPAsyncWebServer-esphome.a
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

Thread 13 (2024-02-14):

Hardware that's verified to work

apolloFER, 2024-02-14:
I just setup my Droplet (second one is on the way). I bought the moisture sensors that were linked in the README. I've compared them to the ones that were available through pricelesstoolkit.com - HW-390 20210603. They're the same.

From what I've read, there's so much stuff around these moisture sensors - different chips, different components, missing timers and resistors. Mine should be "fine" but it's mostly not working.

Calibrated voltage range in the OS (0.99V to 2.5V) is never seen. I've overriden the sensor so it logs the raw voltage it sees and it's in the 0.7V-0.8V range. Fully submersed in water and in dry air - no change (stays at 0.75V +/- 0.03V). When in fully dry soil it increases to almost 0.9V. But the values jump around all the time (+/- 0.05V). The range is narrow. Tried attenuation set to auto as well.

Are there any sensors that are fully verified and that are known to work correctly with Droplet? Or is it a hit and miss until I found some that are working?

Thanks a lot!

PricelessToolkit, 2024-02-14:
The primary issue with the sensors I encountered involves a 1MΩ resistor that is installed but lacks a proper connection, and reading values dropping too slowly, I installed 1MΩ resistors on the droplet board, even if you have no connection on the sensor it will work. The signal pin needs to be connected to ground through this resistor. If the sensor provides a range of "0.7-0.8V", it can be considered non-functional. Additionally, there are two more aspects to check: firstly, the diode installed may sometimes not be the original one but a random diode. Secondly, if you have multimeter compare the capacitor's value as it might be too small, or the 1MΩ resistor is too small, leading to the capacitor discharging too quickly. These sensors were produced by everyone who had a pnp machine :) so yeah its a hit and miss unfortunatly.

apolloFER, 2024-02-15:
Because of this, I would recommend you remove the Aliexpress link for the moisture sensors from the README.

These ones seemed promising to me: https://www.aliexpress.com/item/1005004895663124.html but after going through reviews I noticed some are OK and some were flipped. So not any better than the ones in Readme.

I've ordered these: https://www.aliexpress.com/item/32908693444.html and I'll report back if they're OK. They should have NE555 which is not a great option (TL555C/I is better).

PricelessToolkit, 2024-02-15:
OMG!!! thanks for letting me know.

PS: Should I make my own sample sensors?  but I can't produce with such low prices.

apolloFER, 2024-02-15:
I think the goal is to try to find sensors that are proved to be good. The PCB itself is mostly fine (unless you get the revision with missing 1MΩ GND connection). If you decide to make your own samples, I'd welcome it. But like you said, it's hard to produce them at such low prices. Even if you restock these in your shop (tested ones) it would help a lot.

ruimarinho, 2024-04-12:
@apolloFER any update on your quest to find a reliable moisture sensor :)?

apolloFER, 2024-04-13:
Yeah, I got [these](https://www.aliexpress.com/item/32908693444.html) ones and they have been working well. Those are the v1.2 but have the correct voltage regulator. A friend have me his v2.0 and that one was OK and working but don't know where he bought it.

Now I'm dealing with issues with pumps. I bought 15 of the [linked ones](https://www.aliexpress.com/item/1005005815962951.html) but they have very very poor reliability. 5 have already died (3 of them while I'm away for 3 weeks) so I'll need to find better ones (or a better seller).
Different ones I'm planning to try:

- https://www.aliexpress.com/item/1005005845034014.html
- https://www.aliexpress.com/item/1005005849610603.html
- https://www.aliexpress.com/item/1005005238191161.html
- https://www.aliexpress.com/item/1005006308119076.html
- https://www.aliexpress.com/item/1005005364015831.html
- https://www.aliexpress.com/item/1005005732870398.html

PricelessToolkit, 2024-04-13:
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

Thanks for the links,
are you sure your dead pump is for water? In the past, I bought 20 for water, but it turned out to be for air when I opened it. It didn't have a rubber seal, so water entered the motor and ruined it.

apolloFER, 2024-04-13:
> Thanks for the links, are you sure your dead pump is for water? In the past, I bought 20 for water, but it turned out to be for air when I opened it. It didn't have a rubber seal, so water entered the motor and ruined it.

To be honest, it's more than likely. The Aliexpress description said it's water. But at the same time I've noticed that JQB1523 pumps are usually quoted as air, while JSB1523 are quoted as water. And mine were JQB but quoted as water. I'll try the others that are not JQX models to see if they're better and I'll open up the ones that died when I get back home.
Did you try running pumps that are designed for 3V/3.7V at 5V? I found some that look like the pump you have in video (90 degrees between inlet/outlet ports) but are 3.7V.

PricelessToolkit, 2024-04-13:
> > Thanks for the links, are you sure your dead pump is for water? In the past, I bought 20 for water, but it turned out to be for air when I opened it. It didn't have a rubber seal, so water entered the motor and ruined it.
>
> To be honest, it's more than likely. The Aliexpress description said it's water. But at the same time I've noticed that JQB1523 pumps are usually quoted as air, while JSB1523 are quoted as water. And mine were JQB but quoted as water. I'll try the others that are not JQX models to see if they're better and I'll open up the ones that died when I get back home. Did you try running pumps that are designed for 3V/3.7V at 5V? I found some that look like the pump you have in video (90 degrees between inlet/outlet ports) but are 3.7V.

The label may indicate it's for water, but that's not necessarily the case :). I run them at 5 volts, and the pumps operate for a maximum of 6 seconds at a time. If you need to pump liters of water, they might burn out. Also, when inspecting pumps that have stopped working, please inform us if there is water damage or just burnout.

apolloFER, 2024-04-13:
All of them failed while they were off for a day or two (after they were working). I usually "flush" the system after 30min (to get air through the pumps). My guess is it's going to be water damage and not burnout but I'll report back.

I ordered a bunch of [CJWP12](https://www.aliexpress.com/item/1005005779638400.html) which seem to have backwater prevention feature (also available [here](https://www.aliexpress.com/item/1005005849610603.html) and [here](https://www.aliexpress.com/item/1005005858670203.html)). I'll use them for Droplets 3 and 4 and report back about them.

apolloFER, 2024-04-13:
I did some datasheet googling.

JQB1523 pumps (those linked in README) come in series 1 and series 2 varieties. [Series 1](https://en.symtek.com.tw/wp-content/uploads/sites/2/2019/10/TCS-JQB1523-series1-datasheet.pdf) is an air pump, Series 2 is a vacuum pump (medium not specified, not sure if it's water or not).
[JSB1523](https://en.symtek.com.tw/wp-content/uploads/sites/2/2019/03/JSB1523008.pdf) pumps are water pumps.

I also found the [datasheet](http://www.conjoin.com.cn/upfiles/products/202306/CJWP12-AA.pdf) for the CJWP12 pumps. Those are quieter, use less current, and have comparable flow (80mL/min) + also have backflow protection.

Since JQB are non deterministic in which versions there are, it's better to recommend JSB1523 or CJWP12 pumps. I'll need to confirm if CJWP12 fit in the Droplet 3D case.

PricelessToolkit, 2024-04-13:
Thanks!! I updated the Pump link and uploaded the datasheet.

ruimarinho, 2024-05-13:
Any feedback so far @apolloFER ?

apolloFER, 2024-05-14:
Sort of. I wanted to wait until I can properly test the pumps but I can give an early update.

CJWP12 are OK in size and work as expected. Haven't tried them yet with actual watering. The reason for that is that they come with the wrong connector. They don't have JST XH 2.54 connector but something much smaller. I was able to resolder another wire with a XH 2.54 to test them out. I'm now waiting for a batch of XH 2.54 connectors in order to rewire all the pumps (22 of them) that I got.

Also, they have a smaller inlet/outlet diameter - 3.5mm. So 4mm hoses are out of question. Even 3mm hoses don't give me reassurance that they won't fall out when water pressure kicks in. I'll probably use some acrylic silicone to bond the hose.

apolloFER, 2024-06-25:
Update on the pumps.

I've replaced all the connectors with XH 2.54 so they're working now without problem.

I'm using 3mm hoses but they're also not the tightest fit. So I added some aquarium sillicon to the hose/inlet connection.

I've tested the pump to a height of around 1.5m and it was able to push the water without problem.

Unlike some other pumps, the water doesn't "drain" away when the pumps stop working. Bust be that backwater protection in the pumps themselves. I'm using distilled water so shouldn't cause any issues.

So the pumps themselves are pretty good - probably a bit better than JSB1523 counterparts. But the connector replacement is probably too big of a hassle.

PricelessToolkit, 2024-06-25:
Thank you for the update! Yes, I also think that changing the connector is too big of a hassle. Unfortunately, I can't put $1000 into stocking good quality pumps. If I import them, the selling price will go up 2-3 times without considering my margin.

Closed 2024-11-04.

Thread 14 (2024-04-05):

Soil senor update interval

arne182, 2024-04-05:
Would it be possible to reduce the interval so that home assistant is not overloaded with reading s. Maybe an averaged reading every few seconds is better. Or even every minute would be more than good enough

PricelessToolkit, 2024-04-05:
HI, yes just change "update_interval: xx" for the sensors.
For "COMPARISON SENSOR" and "MOISTUR LEVEL SENSOR" don't put a big number, for example, "2s" means it will pump 2s after reading "sensor value", but if the sensor value does not change 1 minute it will pump 30 times.

# TMP SENSOR #
```c
dallas:  # Integrated Temperature Sensor. https://esphome.io/components/sensor/dallas.html
  - pin: 25
    update_interval: 5s
```

# MOISTUR LEVEL SENSORS #

```c
sensor:
  # MOISTUR LEVEL SENSORS #   https://esphome.io/components/sensor/adc.html?highlight=adc
  - platform: adc
    pin: 34
    id: "Soil1"
    name: "${name} SoilM Sens 1"
    icon: "mdi:water-percent"
    update_interval: 2s
    unit_of_measurement: "%"
    attenuation: 11db
    filters:
    - calibrate_linear:
        - 2.520 -> 0.00  # Calibrate Min in dry soil
        - 0.99 -> 100.00 # Calibrate MAX in 100% wet soil
    - lambda: |
        if (x < 0) return 0;
        else if (x > 100) return 100;
        else return (x);
    accuracy_decimals: 0

```

 # COMPARISON SENSOR #
```c

  - platform: template
    name: "Comparison Sens1"
    internal: true
    update_interval: 2s # Seconds to pump water then stops pumping and starts comparing sensors data, if needed it will pump again
    lambda: |-
      if (id(Soil1).state < id(desired_mois_value_1).state) {
        id(pump1).toggle();
      } else {
        id(pump1).turn_off();
      }
      return {};

```

Closed 2024-04-13.

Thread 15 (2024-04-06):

Can't flash via usb-uart

bernardovalente, 2024-04-06:
Hi,

I lost the encryption key for esphome when I lost the previous HA config. The droplet gets reconized on the new install but I can't give it access to integrate without this key so I'm trying to flash a new config but I'm having trouble with getting it recognized on my w11 desktop.

I'm using a usb to ttl adapter, tried moving the jumper on 3,3v and 5,v  and only connecting:

txd-rxd
rxd-txd
gnd-gnd
vdd-to nothing

and then I followed your guide to manual reflash, with and without external power to the board but it allways fails to open and connect

any tips? thank you

PricelessToolkit, 2024-04-06:
ESP32 has 3.3V Logic Level, so put your USB TTL adapter to 3.3V

Connect TTL adapter to droplet "Don't connect USB yet"
1 ##### USB TTL ######
txd-rxd
rxd-txd
gnd-gnd
vdd-to 3.3V "on pin header for OLED"

2 ############

Push and hold the "PROG button" then Connect the USB to the PC, when programming starts you can release the button.

bernardovalente, 2024-04-24:
I still can't connect to the board it says serial connection refused.
I'm afraid perhaps I messed up the board when connecting both the ttl adapter and the external power or maybe the 5v from the adapter..

I'm going to try on a linux box maybe it's a w11 problem

PricelessToolkit, 2024-04-24:
maybe your TTL adapter just can't supply enough power in 3.3V mode.

bernardovalente, 2024-05-11:
So I changed the TTL adapter and managed to flash a modified droplet.yaml but it can't connect to wifi and only outputs this error continuosly:

`[19:23:04]rst:0x10 (RTCWDT_RTC_RESET),boot:0x13 (SPI_FAST_FLASH_BOOT)
[19:23:04]invalid header: 0x00000000
[19:23:04]invalid header: 0x00000000
[19:23:04]invalid header: 0x00000000
[19:23:04]invalid header: 0x00000000
[19:23:04]invalid header: 0x00000000
[19:23:04]invalid header: 0x00000000
[19:23:04]invalid header: **0x00000000`**

any thoughts?

PricelessToolkit, 2024-05-11:
Hi, YAML is ok,  for programming use https://web.esphome.io/ and for testing use a power supply.

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

The problem could be due to several things
1. Wrong file format "legacy vs modern".
2. Programmed incorrectly.
3. Not enough power.
4.  Domaged with 5V but the probability is very very low.

bernardovalente, 2024-05-31:
I've tried a few configs but after flashing and reseting it, it outputs the same error via usb, also when powered via jack and with a couple of 5v usb chargers it never seems to connect to wifi.

I'm using web.esphome.io and choosing modern.

On your yaml you have:

```
esphome:
  name: ${name}
  name_add_mac_suffix: true
  project:
    name: pricelesstoolkit.droplet
    version: "1.0"

  platform: ESP32
  board: esp32dev
```

perhaps should be?:

```
esphome:
  name: droplet
  friendly_name: Droplet

esp32:
  board: esp32dev
  framework:
    type: xxxxxxxxxxx?
```

PricelessToolkit, 2024-05-31:
The default config working perfectly, it is not a config problem.

Can you try to flash the blink example into the board with Arduino IDE and select those configs for erasing flash completely?

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

And then upload this bin file with "web.esphome" it is my exact config.

[droplet-factory.zip](https://github.com/user-attachments/files/15518438/droplet-factory.zip)

The password is in secret.yaml
```
wifi:
  ssid: !secret wifi_ssid
  password: !secret wifi_password
  fast_connect: true
```

if this does not work for you, [contact me](https://www.pricelesstoolkit.com/en/contact-us) don't forget to add the order number.

bernardovalente, 2024-06-29:
I'm trying the bare mininum example because it coudn't compile the blink one but I'm getting this error:

```
Sketch uses 266169 bytes (20%) of program storage space. Maximum is 1310720 bytes.
Global variables use 20184 bytes (6%) of dynamic memory, leaving 307496 bytes for local variables. Maximum is 327680 bytes.
esptool.py v4.6
Serial port COM5
Connecting.......
Chip is ESP32-D0WDQ6-V3 (revision v3.0)
Features: WiFi, BT, Dual Core, 240MHz, VRef calibration in efuse, Coding Scheme None
Crystal is 40MHz
MAC: 30:c6:f7:22:87:bc
Uploading stub...
Running stub...
Stub running...
Changing baud rate to 921600
Changed.
Configuring flash size...
Erasing flash (this may take a while)...
Chip erase completed successfully in 0.0s
Compressed 19744 bytes to 13604...
Writing at 0x00001000... (100 %)
Wrote 19744 bytes (13604 compressed) at 0x00001000 in 0.4 seconds (effective 363.8 kbit/s)...
File  md5: 9fef1c1dc138cc0789ab3580d40b7b3e
Flash md5: ab5728dbeeb6fc465c6bbc16dad27590
MD5 of 0xFF is 5141cba2467248253063971ed8466710

A fatal error occurred: MD5 of file does not match data in flash!
Failed uploading: uploading error: exit status 2
```

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

PricelessToolkit, 2024-06-29:
Ok, let's fix that!

1. **Check Python Installation**: Open CMD and type `python`, then press Enter. If you see output like `Python 3.9....`, Python is installed.

2. **Install Python**: If not installed, download and install the latest Python version, and ensure to check "Add Python to PATH".

   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

3. **Install esptool**: Open CMD and type:

 ```sh
pip install esptool
```

Erase Flash: Run the following command, replacing COM4 with your port:
 ```sh
python -m esptool --chip esp32 --port COM4 --baud 115200 --after hard_reset erase_flash
```
Write Flash Status: Run:

```sh
python -m esptool --chip esp32 --port COM4 write_flash_status --non-volatile 0
```
Disconnect and reconnect the power

This should fix the problem!

PricelessToolkit, 2024-06-29:
Then,  Skip the Arduino IDE part and try flashing ESPHome.

bernardovalente, 2024-06-30:
So I ran the commands and then flashed the droplet.bin, everything went fine but It still didn't connect when powered by the 5v barrel and it gives the same error in the logs when connected by usb. I also tried a basic esphome config and it still didn't work.
Any thing else I can try?

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

PricelessToolkit, 2024-06-30:
Unfortunately, the only solution in this case is to replace the ESP32 module. sorry!

PricelessToolkit, 2024-07-04:
"ESP32 ESP-WROOM-32" https://fr.aliexpress.com/item/32899182878.html

PricelessToolkit, 2024-07-04:
If you live in Europe, you can send it to me and I will repair it for free.

PricelessToolkit, 2024-07-04:
https://www.lcsc.com/product-detail/WiFi-Modules_Ai-Thinker-ESP32-S_C277944.html

bernardovalente, 2024-07-13:
I ordered an esp32 replacement that I'll try and replace it myself, it's arriving soon, but it's great to know that you might be able to do something to perhaps repair it, I might take you on that offer.

Awesome, thank you! I'll get back to you soon.

Closed 2024-11-04.

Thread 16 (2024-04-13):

Water source

ruimarinho, 2024-04-13:
Hi,

I’m very interested in this project and I’m just waiting for restocking to help support it as well.

I’m wondering what’s the expected water source? A water bucket? I’d like to have this connected directly to a faucet but it would need some kind of pressure control. Any suggestions?

Thanks for the tips!

apolloFER, 2024-04-13:
I use it with a 7L water bottle. But I'm also planning to get one of those large [25L containers](https://cdn3.jysk.com/getimage/wd2.large/113092) (drill holes for hoses). No idea on connecting it directly to a faucet - you might be able to do it with the extension board and some relays (to prefill another large container when it empties).

PricelessToolkit, 2024-04-13:
Hi, you can use a bucket and valve like in toilets with a float to auto-refill.

ruimarinho, 2024-04-13:
Or what @PricelessToolkit said 🤣 away with precision level meters and just use a mechanical valve which is much safer!

Closed 2024-04-16.

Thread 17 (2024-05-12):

Is it ok to use pump motors on 3v?

stefancvetkovic, 2024-05-12:
Hello, your aliexpress link points to water pumps on 3V, model A, but you said that motor pumps should be on 5v?

Can you please provide some additional links for buying these motors? Thanks

PricelessToolkit, 2024-05-12:
It is one link but in the shop, there are 2 versions, Model "B JSB1523" is 5V Model "A JQB1523" is 3V. Datasheet https://github.com/PricelessToolkit/Droplet/blob/main/Water_Pump_JSB1523008.pdf

stefancvetkovic, 2024-05-13:
Yes, I know that there are two models A and B, one operates on 5v and other on 3v.
Regarding the 3D case and your youtube demo video, I would say that I need model A, which operates on 3V?

But you said in readme.md file:
5x Micro Pump outputs "5v"

So as far I can see I have two options:
1. use model B (parallel water nozzles), but then I will need to edit just a little bit 3D model for the housing
**OR**
2. use model A and not to be worried because it operates on 3v?

Thanks,

PricelessToolkit, 2024-05-13:
you dont need to modify anything it is the same size. use 5v version.

stefancvetkovic, 2024-05-13:
so your recommendation is to use type B  water pump on 5v?
Your design of enclosure is designs to support type A water pumps, nevertheless, I mount type B, and it works just fine, I will then just do another casing for this type of water pumps

PricelessToolkit, 2024-05-13:
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

There is no difference between Type A or B; when you screw the lid, it holds both Type A and B pumps.

stefancvetkovic, 2024-05-13:
Ok, I will let then leave it as is. Model B motors (parallel nozzles) on 5V. Thanks!

Closed 2024-11-04.

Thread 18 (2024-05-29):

Detailed specs for extension board v3

stefancvetkovic, 2024-05-29:
It would be nice if there is any BoM file preferably for DigiKey or LCSC electronic part numbers, in order to be easier to find those components.
Also is tyhere an option to order expansuion board? thanks

PricelessToolkit, 2024-05-29:
Hi, I added the possibility of ordering an extension board only and uploaded BOM for the expansion board with supplier part numbers.

Closed 2024-05-29.

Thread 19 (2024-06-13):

3D case for expansion board also

stefancvetkovic, 2024-06-13:
Hello,
I'm wondering do you have 3D case that is completely done including expansion board also?
I was thinking to start to edit current 3D model, and to have the case for expansion board also.
Thanks

PricelessToolkit, 2024-06-13:
Hi, do you mean cover for expansion? I didn't make a closed version.

Closed 2024-06-13.

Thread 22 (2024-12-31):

Pumps turning off immediately after turning on

avrabi19, 2024-12-31:
When I use the physical buttons they work fine but when I send a command through home assistant they immediately turn back off

avrabi19, 2024-12-31:
I am using the pumps used linked 5 volt

PricelessToolkit, 2025-01-01:
It is normal behavior with current yaml

```yaml

- platform: template
  name: Comparison Sens1
  internal: true
  update_interval: 2s   # Seconds to pump water then stops pumping and starts comparing sensors data, if needed it will pump again
  lambda: |-
    if (id(Soil1).state < id(desired_mois_value_1).state) {
      id(pump1).toggle();
    } else {
      id(pump1).turn_off();
    }
    return {};

```

avrabi19, 2025-01-01:
Oh ok thanks so I have to write my own yaml and set that in a trigger?

PricelessToolkit, 2025-01-01:
If you want all the logic in HA, yes. In the current YAML, the on and off logic is defined in YAML. It takes the max level value from HA, compares it with the sensor value, and then decides if the pump needs to be on or off.

avrabi19, 2025-01-01:
Awesome! Thanks for the very fast help Loving the board. I will probably order a second one in a month or two

Closed 2025-01-01.

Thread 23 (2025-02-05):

JQB1523 link is not available.

JohnMcLear, 2025-02-05:
Looks like https://www.aliexpress.com/item/1005005601497176.html is the new link

one thing to note is it does appear that the wired(+,-,Data) connector has changed to a smaller pitch connector.  we should probably document what pitch you'll want for pumps?  Afaik pin pitch is XH 2.54MM as per docs.  -- the docs do specify needing some cables but it's not really clear that they are needed for this.

https://www.aliexpress.com/item/1005005815962951.html appears to also be okay and the right size connector but liquid connections are in a different place.

PricelessToolkit, 2025-02-05:
Thanks for letting me know. The link has been updated, and I’ve added information about the 2.54 mm connector as well.

JohnMcLear, 2025-02-07:
Thanks man!

Closed 2025-02-07.

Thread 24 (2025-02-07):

pH sensor

JohnMcLear, 2025-02-07:
I'm using GPIO39 / Soil5 for pH

```
- platform: adc
  pin: GPIO39
  name: "pH"
  update_interval: 60s
  unit_of_measurement: pH
  # https://esphome.io/components/sensor/index.html#sensor-filters
  filters:
    - median:
        window_size: 7
        send_every: 4
        send_first_at: 3
    # Measured voltage -> Actual pH (buffer solution)
    - calibrate_linear:
        - 1.55 -> 7.0
        - 2.09 -> 4.0
  attenuation: auto
```

I removed all ref to ``Soil5``

Is this the cleanest way to do this?  Should there be a cleaner way?

PricelessToolkit, 2025-02-07:
Hi, your config is normal, just change the name part to

```yaml
name: ${name} pH
```

PS: which pH sensor do you plan to use?

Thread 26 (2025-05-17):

I cant connect it to HA reconnects every 4.30min

stefancvetkovic, 2025-05-17:
Hello,

I have strange behavior the board connects to my wifi, but recconects every 4min and 30 seconds.

DO you know why is that?

Also, I'm unable to connect it to my HA, saying Unable to connect to the ESPHome device. Make sure the device’s YAML configuration includes an `api` section.

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

here is my code:
https://pastebin.com/9MDnyXEV

PricelessToolkit, 2025-05-17:
Hi,

1. You need to include the API https://esphome.io/components/api.html
2. When you connect it to HA, open the wireless log, and we will see what's going on.

stefancvetkovic, 2025-05-17:
1. I already have `api:`  part, but I added now
```encryption:
  key: xxxx
```

2.But I can't connect it to the HA, that's the issue. Maybe firstly I can try to access it directly to captive portal?

PricelessToolkit, 2025-05-18:
If it has original firmware "not reflashed", then the current way is to configure it through the captive portal.

stefancvetkovic, 2025-05-18:
No, it doesn't have.
I flashed it a year ago, and it worked, and now it doesn't work (not being in production for several months)
Can I ship back to you this device and you can check it? Or something like that?
I presume that default firmware is the one that you posted in ESPHOME folder for configuration?
-

PricelessToolkit, 2025-05-21:
No need to resend, Just erase memory with Arduino IDE, check "Erase full memory before sketch upload," and upload a blank sketch. Then flash with ESPHome, and it will work.

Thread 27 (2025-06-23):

Pump recommendation not matching screenshot & 3D model

nstrelow, 2025-06-23:
Some time ago I bought this very cool board and the pumps recommended in the description:

"Water Pump "Model B JSB1523" 5V "Connector pitch 2.54mm" - https://s.click.aliexpress.com/e/_ok8vbDj"

This pump has 2 tube connection that go out the bottom.

The screenshot show something looking like the other "Model A" that is 3.7V and has one tube coming out of the front of the pump.

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

I bought probably the wrong pump (did buy it probably 3 years back): "CM1135T-UL"

It's width is 21 mm, which seems to be the same as the pump linked on Aliexpress. With that pump the house does not fit perfectly, the gap seems too small.

I am wondering if there are any up to date pictures using the 2 tube connections at the bottom pump?

Are there any recommendations to hold the pump in place, if attached to a wall? Maybe hotglue them?

Thanks and have a great week 😀

PricelessToolkit, 2025-06-23:
Hi, I can't find the picture of the pump "CM1135T-UL", so I can't say anything about that. Normally, if you are using a 3D printed case and you tighten the bolts, it holds the pumps in place. If your pump is smaller, you can add some double-sided tape.

Have a nice weekend.

nstrelow, 2025-06-24:
The pump is slightly bigger, but should be the same height & width as the Model B.

I am curious, was there any reason for the shift from pump shown in the picture to the recommended one where the 2 pump outlets are on the same side?

Thanks in any case for this cool board and all the best with your other cool projects 😁

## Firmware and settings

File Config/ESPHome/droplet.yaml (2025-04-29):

substitutions:
  name: droplet

esphome:
  name: ${name}
  name_add_mac_suffix: true
  project:
    name: pricelesstoolkit.droplet
    version: "1.0"
    
  on_boot:
    priority: -100
    then:
      - lambda: id(oled).turn_off();

esp32:
  board: esp32dev

dashboard_import:
  package_import_url: github://PricelessToolkit/Droplet/Config/ESPHome/droplet.yaml@main
  import_full_config: true


# Enable logging
logger:

ota:
- platform: esphome
  password: bfec11234xsfea57e1b5d3b985cfe06c

wifi:
  ssid: !secret wifi_ssid
  password: !secret wifi_password
  fast_connect: true
  # domain: .lab.lan # if you have custom domain not .local

  # Enable fallback hotspot (captive portal) in case wifi connection fails
  ap:
    ssid: ${name} Fallback Hotspot
    password: password

captive_portal:

one_wire: #https://esphome.io/components/one_wire
- platform: gpio
  pin: GPIO25

i2c: # i2c Pins
  sda: 21
  scl: 22
  scan: true

mcp23017: # Expansion Board  https://esphome.io/components/mcp230xx.html
- id: mcp23017_hub
  address: 0x20

font: # Fonts for Display
- file: arial.ttf
  id: font1
  size: 8
- file: arial.ttf
  id: font2
  size: 10
- file: arial.ttf
  id: font3
  size: 14

display: # More info https://esphome.io/components/display/ssd1306.html?highlight=1306         
- platform: ssd1306_i2c
  id: oled
  model: SSD1306 128x64
  address: 0x3C   # Oled Display Address
  lambda: |-
    it.printf(2, 0, id(font2), TextAlign::TOP_LEFT, "DROPLET");
    it.printf(61, 0, id(font2) ,"%.1f", id(dbm).state);
    it.line(0, 12, 98, 12);
    it.line(98, 0, 98, 64);
    it.printf(102, 0, id(font2) ,"%.1f", id(Soil1).state);
    it.printf(102, 12, id(font2) ,"%.1f", id(Soil2).state);
    it.printf(102, 24, id(font2) ,"%.1f", id(Soil3).state);
    it.printf(102, 36, id(font2) ,"%.1f", id(Soil4).state);
    it.printf(102, 48, id(font2) ,"%.1f", id(Soil5).state);
#    it.printf(5, 15, id(font3) ,"%.1f°C", id(intergratedtmp).state);
#    it.printf(5, 30, id(font3) ,"%.1fH", id(dhthumidity).state);
#    it.printf(5, 45, id(font3) ,"%.1fP", id(pressure).state);


  # Integrated BUZZER # If you using pin23 for something else, delete this and remove jumper 1

rtttl:
  output: rtttl_out
  on_finished_playback:
  - logger.log: Song ended!

api:
  services:
  - service: play_rtttl
    variables:
      song_str: string
    then:
    - rtttl.play:
        rtttl: !lambda 'return song_str;'

            # https://esphome.io/components/rtttl.html
            # In the developer tools. E.g. for calling rtttl.play select the service droplet_play_rtttl and in service data enter    siren:d=8,o=5,b=100:d,e,d,e,d,e,d,e   or  scale_up:d=32,o=5,b=100:c,c#,d#,e,f#,g#,a#,b  


sensor:
  # MOISTUR LEVEL SENSORS #   https://esphome.io/components/sensor/adc.html?highlight=adc
- platform: adc
  pin: 34
  id: Soil1
  name: ${name} SoilM Sens 1
  icon: mdi:water-percent
  update_interval: 2s
  unit_of_measurement: '%'
  attenuation: 12db
  filters:
  - calibrate_linear:
    - 2.520 -> 0.00      # Calibrate Min in dry soil
    - 0.99 -> 100.00     # Calibrate MAX in 100% wet soil 
  - lambda: |
      if (x < 0) return 0; 
      else if (x > 100) return 100;
      else return (x);
  accuracy_decimals: 0

- platform: adc
  pin: 35
  id: Soil2
  name: ${name} SoilM Sens 2
  icon: mdi:water-percent
  update_interval: 2s
  unit_of_measurement: '%'
  attenuation: 12db
  filters:
  - calibrate_linear:
    - 2.520 -> 0.00      # Calibrate Min in dry soil
    - 0.99 -> 100.00     # Calibrate MAX in 100% wet soil 
  - lambda: |
      if (x < 0) return 0; 
      else if (x > 100) return 100;
      else return (x);
  accuracy_decimals: 0

- platform: adc
  pin: 32
  id: Soil3
  name: ${name} SoilM Sens 3
  icon: mdi:water-percent
  update_interval: 2s
  unit_of_measurement: '%'
  attenuation: 12db
  filters:
  - calibrate_linear:
    - 2.520 -> 0.00      # Calibrate Min in dry soil
    - 0.99 -> 100.00     # Calibrate MAX in 100% wet soil 
  - lambda: |
      if (x < 0) return 0;
      else if (x > 100) return 100;
      else return (x);
  accuracy_decimals: 0

- platform: adc
  pin: 33
  id: Soil4
  name: ${name} SoilM Sens 4
  icon: mdi:water-percent
  update_interval: 2s
  unit_of_measurement: '%'
  attenuation: 12db
  filters:
  - calibrate_linear:
    - 2.520 -> 0.00      # Calibrate Min in dry soil
    - 0.99 -> 100.00     # Calibrate MAX in 100% wet soil 
  - lambda: |
      if (x < 0) return 0;
      else if (x > 100) return 100;
      else return (x);
  accuracy_decimals: 0
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

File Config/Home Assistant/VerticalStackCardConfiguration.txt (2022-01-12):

type: vertical-stack
cards:
  - type: horizontal-stack
    cards:
      - type: vertical-stack
        cards:
          - type: entities
            entities:
              - input_number.moisture_level_for_pump1
          - type: sensor
            entity: sensor.droplet_soilm_sens_1
            graph: line
      - type: vertical-stack
        cards:
          - type: entities
            entities:
              - input_number.moisture_level_for_pump2
          - type: sensor
            entity: sensor.droplet_soilm_sens_2
            graph: line
  - type: horizontal-stack
    cards:
      - type: vertical-stack
        cards:
          - type: entities
            entities:
              - input_number.moisture_level_for_pump3
          - type: sensor
            entity: sensor.droplet_soilm_sens_3
            graph: line
      - type: vertical-stack
        cards:
          - type: entities
            entities:
              - entity: input_number.moisture_level_for_pump4
          - type: sensor
            entity: sensor.droplet_soilm_sens_4
            graph: line
  - type: entities
    entities:
      - input_number.moisture_level_for_pump5
  - type: sensor
    entity: sensor.droplet_soilm_sens_5
    graph: line

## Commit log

2021-12-31 added Comments in esphome config
    [Assem.SLDASM, Assem_Cover_full.SLDASM, Cover_full_Part.SLDPRT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]
2022-01-11 Project Update
    [Assem.SLDASM, Housing_battom.SLDPRT, Pump_Holder_Down.STL]
2022-01-11 STL Update
    [Pump_Holder_Down.STL, Pumps_Holder.STL]
2022-12-28 Added Status and Uptime sensors
2023-01-23 Temp Sensor How To
2023-01-23 commented out dallas sensor (to automatically display sensor address in the terminal)
2023-08-03 Update README.md
    Pumps Link update "The seller changed the water pump to air"
2024-04-13 Update README.md
    Pump Link + water pump datasheet
2024-04-13 Water Pump Datasheet
2024-11-04 Update droplet.yaml
    By default, sensors are commented out.
